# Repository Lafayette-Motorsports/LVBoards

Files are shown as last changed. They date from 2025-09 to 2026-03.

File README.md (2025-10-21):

# MotorsportsLVBoards

LV Board repository for Motorsports created 09.02.2025  

## BE SURE TO COMMIT & PUSH ALL CHANGES WHEN FINISHED TO KEEP THINGS UPDATED  

## Modulation
LV Boards are now 'modulated' - this means that each board is designed to serve a single purpose so that individual circuits/functions can be easily replaced  
    This means that wires need to be obviosuly labeled with their purpose and output params/types to keep things 'open source' enough that it can be easily updated -- keep documentation (wiring diagram, code comments, standalone documentation) updated, descriptive, and accurate  

## If this is your first time
To use this and work on the board (non cmd because if you don't know this you don't need to be trying to do it on the console):  
    - make a github account   
        - you can do this with your school email or your personal but if you plan on making changes, make your screen name traceable (eg. we want to be able to know who's doing stuff)  
    - download github for desktop (https://desktop.github.com/download/) and sign in  
    - 'follow' this repository to add it to your account  
    - click current repository (top left) --> add --> clone repository --> pull origin  
    - find your file path (repository --> show in explorer) and open whatever you want  
    - if you make changes, YOU NEED TO MANUALLY UPDATE THE REPOSITORY, ALL CHANGES MADE ARE LOCAL UNTIL THIS IS DONE  
        - go back to your github app and open the repository (its probably still open), add a summary and commit your changes, push to origin  
        - MAKE YOUR SUMMARY SOMEWHAT DETAILED, YOU DON'T NEED A PARAGRAPH BUT THIS IS A REALLY GOOD PLACE TO PUT A CHANGE LOG SO WE CAN TRACK WHATS HAPPENING WHEN AND GET A SOMEWHAT DETAILED HISTORY  

## Component Cacheing
When adding parts, store them as project-specific rather than global. You will need to create your own library for the project, but you should really only need to do it once per KiCad project -- this will make sure that projects are actually portable. Some projects were built without this in mind so be weary when trying to modify/process files -- they might not have footprints/symbols for every part. If you can't figure out how to do this (or you think you added a symbol but it's not working, footprint not loading, etc.) google it or ask -- the whole point of the GitHub is portability so its kind of stupid to ignore this.

for repository admin (or other) questions - Sean McLoughlin mclougsm@lafayette.edu

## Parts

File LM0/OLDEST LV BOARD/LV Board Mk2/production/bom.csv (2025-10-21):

Designator | Footprint | Quantity | Value | LCSC Part #
C1, C2, C3, C8 | CAP_CL32_SAM | 4 | 47u
C10, C11, C12, C17, C19, C9 | 0603 | 6 | 4.7u
C13, C14, C15, C16 | 1210 | 4 | 47u
C18, C31, C32, C33, C34, C35, C36, C37, C38, C4, C5, C6 | 1206 | 12 | 0.1u
C20, C21, C22 | 0603 | 3 | 22u
C23, C24, C25 | 1210 | 3 | 100u
C26 | 0603 | 1 | 0.22u
C27, C29, C30 | 0603 | 3 | 0.1n
C28 | 0603 | 1 | 27n
C7 | 1206 | 1 | 10u
CR1 | ZENER_Pair_15-5V_clamp | 1 | ESD12VD3B-TP
D1 | SOD323F_DIO | 1 | BZV55B15
D10, D11, D17, D18, D2, D3, D4, D5, D9 | Test-Yellow LED | 9 | LED (Test)
D12, D19, D20, D21, D22, D6 | D_DO-41_SOD81_P10.16mm_Horizontal | 6 | 1N4001
D13, D14, D7, D8 | IMD_ZENER | 4 | D_Zener
D15 | DIO_DFLS1100-7 | 1 | DFLS1100-7
D16 | POWERDI-123 | 1 | DFLS160Q-7
F1 | C1_BEL | 1 | C1Q 2A
F2 | FUSC6125X279N | 1 | 20A
H1, H2, H3, H4, H5, H6 | MountingHole_4mm_Pad_TopBottom | 6 | MountingHole_Pad
J1, J13, J14, J5, J6 | MOLEX_460150202 | 5 | Conn_01x02_Pin
J10, J11, J12, J15, J7, J8, J9 | PinHeader_1x02_P2.54mm_Vertical | 7 | Conn_01x02
J16 | PinHeader_1x02_P2.54mm_Vertical | 1 | Conn_01x02_Pin
J2, J3, J4 | AMPHENOL_L717SDA15P1ACH4F | 3 | L717SDA15P1ACH4F
K1 | RELAY_G6L-1P_DC5 | 1 | G6L-1P_DC5
K2 | RELAY_ALF1PF12 | 1 | ALF1PF12
K3, K4 | AHES4_PAN | 2 | AHES4291
L1 | glv_charge_inductor | 1 | 6.2u
MOSFET1, MOSFET2, MOSFET3, MOSFET4 | fan_driver | 4 | DMN3404L-7
Q1, Q2, Q3, Q4, Q5, Q6 | SOT23_INF | 6 | AON6411
R1, R10, R11, R13, R14, R15, R18, R21, R23, R27, R47, R50, R53, R56, R9 | 0603 | 15 | 10k
R12, R20, R22 | 0805 | 3 | 150R
R16, R17, R24, R25, R48, R49, R5, R51, R52, R54, R55, R57, R58, R6, R7, R8 | 0603 | 16 | 1k
R19 | 0603 | 1 | 2.2k
R2, R4 | 0603 | 2 | 57.6k
R26 | 0603 | 1 | 3.01k
R28, R29, R30, R31 | 1206 | 4 | 120
R3 | 0805 | 1 | 22k
R32 | 1206 | 1 | 0R
R33 | 0603 | 1 | 50k
R34 | 10m_sense | 1 | LVK12R010CER
R35, R36 | 0603 | 2 | 12k
R37, R42 | 0603 | 2 | 549k
R38 | 0603 | 1 | 86.6k
R39, R43, R44 | 1206 | 3 | 500k
R40 | 0603 | 1 | 113k
R41 | 0603 | 1 | 2.91k
R45, R46 | 1206 | 2 | 215k
SW1 | SW4_1825910-B_TEC | 1 | Test Reset IMD
SW2 | SW4_1825910-B_TEC | 1 | Test Reset AMS
TP1, TP2, TP3, TP4, TP5, TP6, TP7, TP8 | TestPoint_Loop_D2.60mm_Drill1.6mm_Beaded | 8 | TestPoint
U1, U2 | SOIC-8_3.9x4.9mm_P1.27mm | 2 | NE555D
U10, U12, U14, U16 | motorsports_senior_design_opto | 4 | TLP2745TP_E
U11, U13, U15, U9 | DBV5_TEX | 4 | UCC27517DBVR
U3 | REG_LT1117IST-5#PBF | 1 | LT1117-5.0
U4, U5, U6 | MOSFET_INFET | 3 | SI7116DN-T1-E3
U7 | UFD_28_ADI | 1 | LTC4013EUFD-TRPBF
U8 | LM324PWR | 1 | LM324PWR

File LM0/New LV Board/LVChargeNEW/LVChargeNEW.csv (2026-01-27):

Reference | Qty | Value | DNP | Exclude from BOM | Exclude from Board | Footprint | Datasheet
C1 | 1 | 1uF |  |  |  | Capacitor_THT:CP_Radial_D8.0mm_P5.00mm | ~
C2,C3 | 2 | 4.7uF |  |  |  | Capacitor_THT:CP_Radial_D8.0mm_P5.00mm | ~
C4,C6,C7 | 3 | 100uF |  |  |  | Capacitor_THT:CP_Radial_D8.0mm_P5.00mm | ~
C5,C9,C12,C16 | 4 | 80uF |  |  |  | Capacitor_THT:CP_Radial_D8.0mm_P5.00mm | ~
C8,C15 | 2 | 470nF |  |  |  | Capacitor_THT:CP_Radial_D8.0mm_P5.00mm | ~
C10,C11,C13,C14 | 4 | 100nF |  |  |  | Capacitor_THT:CP_Radial_D8.0mm_P5.00mm | ~
C_sys1,C_sys2,C_sys3,C_sys4,C_sys5,C_sys6,C_sys7,C_sys8,C_sys9 | 9 | 100u |  |  |  | Capacitor_SMD:C_1210_3225Metric_Pad1.33x2.70mm_HandSolder | ~
D1,D2,D3 | 3 | LED |  |  |  | LED_SMD:LED_1206_3216Metric | ~
J1,J2 | 2 | Conn_01x02 |  |  |  |  | ~
J3 | 1 | Conn_01x05_Socket |  |  |  | Connector_PinSocket_1.27mm:PinSocket_1x06_P1.27mm_Vertical | ~
L2 | 1 | SRP1770TA-150M |  |  |  | LVChargeNEWLocalFootprints:SRP1770TA_150M | SRP1770TA-150M
Q1,Q2,Q3,Q4 | 4 | CSD15380F3T |  |  |  | LVChargeNEWLocalFootprints:IAUZ20N08S5L300ATMA1
R1,R4 | 2 | 100k |  |  |  | Resistor_THT:R_Axial_DIN0204_L3.6mm_D1.6mm_P5.08mm_Horizontal | ~
R2 | 1 | 53.8k |  |  |  | Resistor_THT:R_Axial_DIN0204_L3.6mm_D1.6mm_P5.08mm_Horizontal | ~
R3 | 1 | 85.4k |  |  |  | Resistor_THT:R_Axial_DIN0204_L3.6mm_D1.6mm_P5.08mm_Horizontal | ~
R5 | 1 | 2.4 |  |  |  | Resistor_THT:R_Axial_DIN0204_L3.6mm_D1.6mm_P5.08mm_Horizontal | ~
R6 | 1 | 5.24k |  |  |  | Resistor_THT:R_Axial_DIN0204_L3.6mm_D1.6mm_P5.08mm_Horizontal | ~
R7,R8,R10,R11 | 4 | 10 |  |  |  | Resistor_THT:R_Axial_DIN0204_L3.6mm_D1.6mm_P5.08mm_Horizontal | ~
R9 | 1 | 30.31k |  |  |  | Resistor_THT:R_Axial_DIN0204_L3.6mm_D1.6mm_P5.08mm_Horizontal | ~
R12,R13,R20 | 3 | 249k |  |  |  | Resistor_THT:R_Axial_DIN0204_L3.6mm_D1.6mm_P5.08mm_Horizontal | ~
R14 | 1 | 133k |  |  |  | Resistor_THT:R_Axial_DIN0204_L3.6mm_D1.6mm_P5.08mm_Horizontal | ~
R15,R16,R17,R18 | 4 | 10k |  |  |  | Resistor_THT:R_Axial_DIN0204_L3.6mm_D1.6mm_P5.08mm_Horizontal | ~
R19 | 1 | 2.6K |  |  |  | Resistor_THT:R_Axial_DIN0204_L3.6mm_D1.6mm_P5.08mm_Horizontal | ~
R_bat_ac1,R_bat_sns1 | 2 | .005 |  |  |  | LVChargeNEWLocalFootprints:RESC2012X80N | ~
U1 | 1 | PQ25856QWRRVRQ1 |  |  |  | LVChargeNEWLocalFootprints:Q25856QWRRVRQ1 | https://www.ti.com/lit/gpn/bq25856-q1

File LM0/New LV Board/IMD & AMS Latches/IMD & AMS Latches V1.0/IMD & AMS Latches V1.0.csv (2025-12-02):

Reference | Qty | Value | DNP | Exclude from BOM | Exclude from Board | Footprint | Datasheet
D1,D2,D5,D6 | 4 | 1N4743A |  |  |  | motorsports:D_DO-41_SOD81_P3.81mm_Vertical_AnodeUp | ~
D3,D7 | 2 | 1N4001 |  |  |  | Diode_THT:D_DO-41_SOD81_P10.16mm_Horizontal | http://www.vishay.com/docs/88503/1n4001.pdf
D4,D8 | 2 | LED (Test) |  |  |  | LED_THT:LED_D3.0mm | ~
J2 | 1 | B12B-PH-K-S |  |  |  | Connector_JST:JST_PH_B12B-PH-K_1x12_P2.00mm_Vertical | B12B-PH-K-S
K1,K2,K3,K4,K5,K6 | 6 | A161CS12VDC.64 |  |  |  | motorsports:RELAY_A161CS12VDC.64
R1,R2 | 2 | 680 |  |  |  | Resistor_THT:R_Axial_DIN0207_L6.3mm_D2.5mm_P2.54mm_Vertical | ~
R3,R4 | 2 | 2.2k |  |  |  | Resistor_THT:R_Axial_DIN0207_L6.3mm_D2.5mm_P2.54mm_Vertical | ~
SW1,SW2 | 2 | Test Reset IMD |  |  |  | motorsports:pushButton | ~

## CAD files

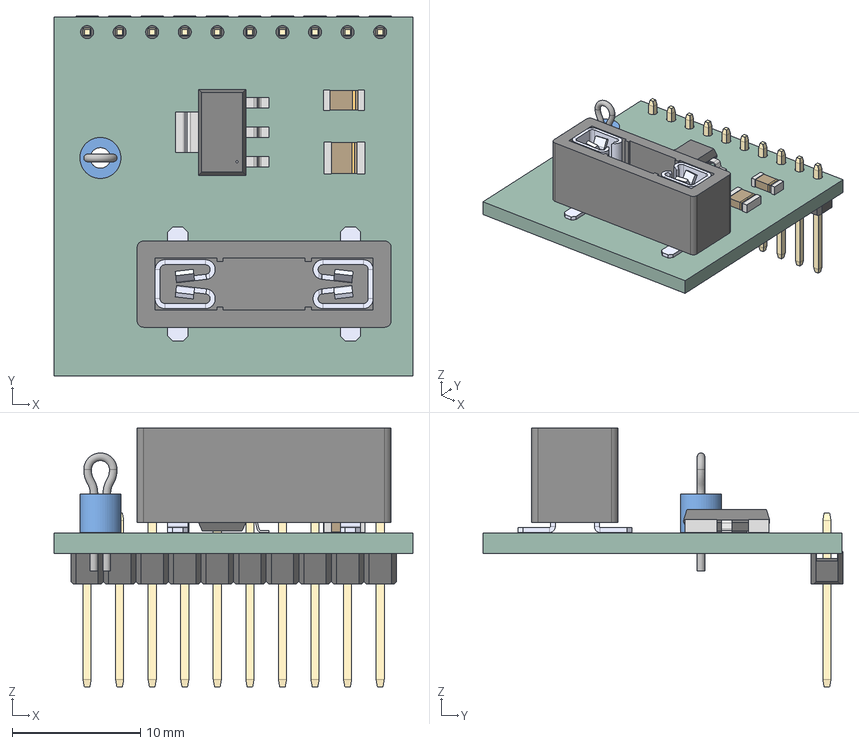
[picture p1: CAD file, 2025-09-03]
5V Converter/5V Converter V1.0/5V Converter.step
28.0 x 28.1 x 20.2 mm
TestPoint_Loop_D2_60mm_Drill1_6mm_Beaded_cp
3587TR
1x10 Male Pin Header
5V Converter_PCB

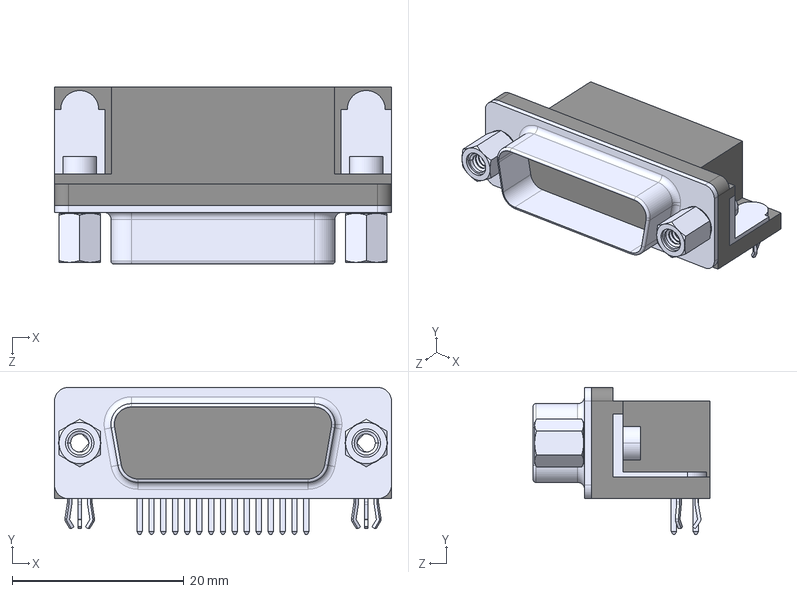
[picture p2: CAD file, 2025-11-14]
LM0/New LV Board/I-O Board V3.0/3d models/L717SDA15P1ACH4F--3DModel-STEP-554624.STEP
39.2 x 17.1 x 20.6 mm

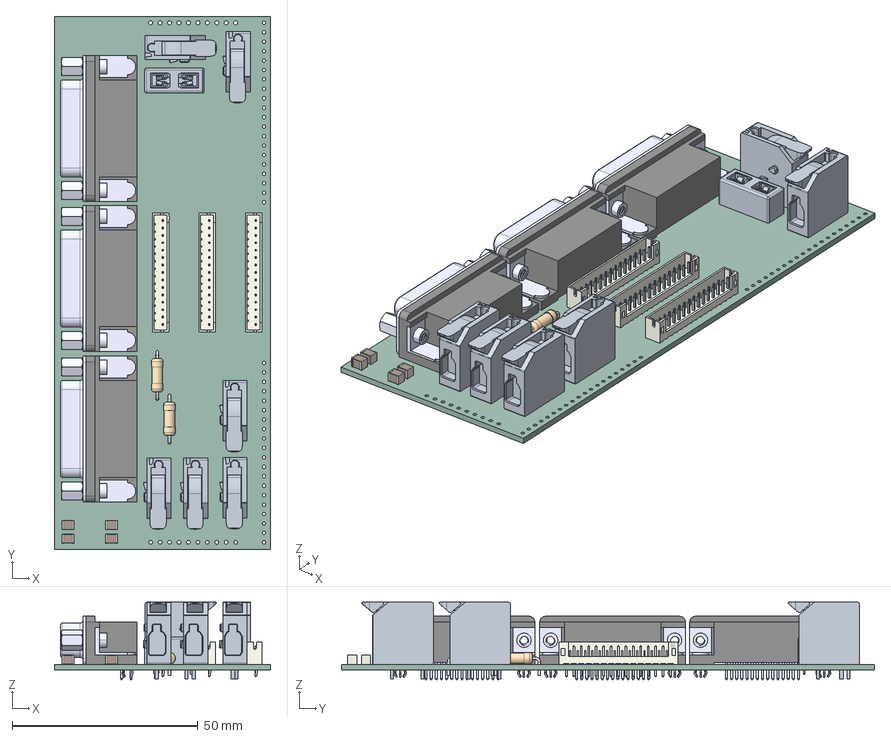
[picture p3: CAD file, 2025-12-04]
LM0/New LV Board/I-O Board V3.0/I-O Board V3.0.step
58.1 x 143.4 x 20.9 mm
C_1210_3225Metric x 4
JST_PH_B15B-PH-K_1x15_P2.00mm_Vertical x 3
l717sdxxxp1ach4f Body _15 x 3
R_Axial_DIN0309_L9.0mm_D3.2mm_P12.70mm_Horizontal x 2
F3568-1
3557_rev.C x 2
I-O Board V3.0_PCB

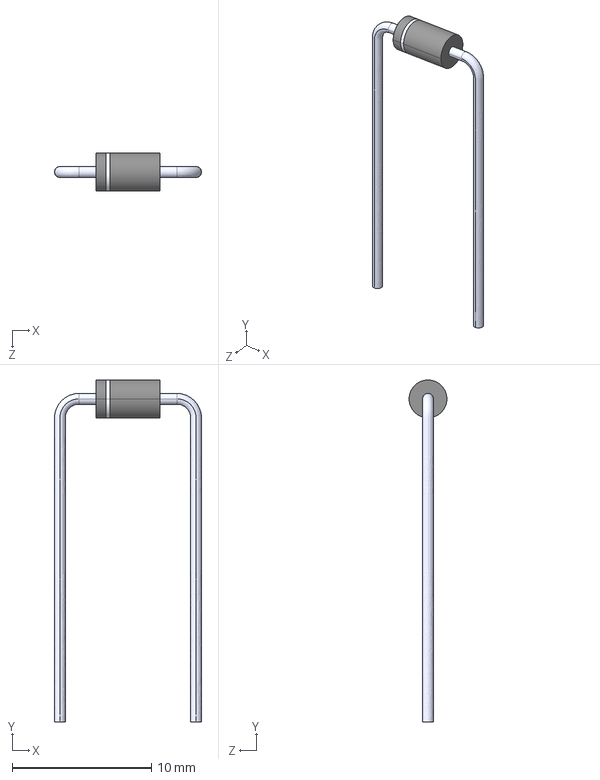
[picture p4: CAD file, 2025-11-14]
LM0/New LV Board/IMD & AMS Latches/IMD & AMS Latches V1.0/3d Models/1N4743A.step
10.6 x 24.6 x 2.72 mm

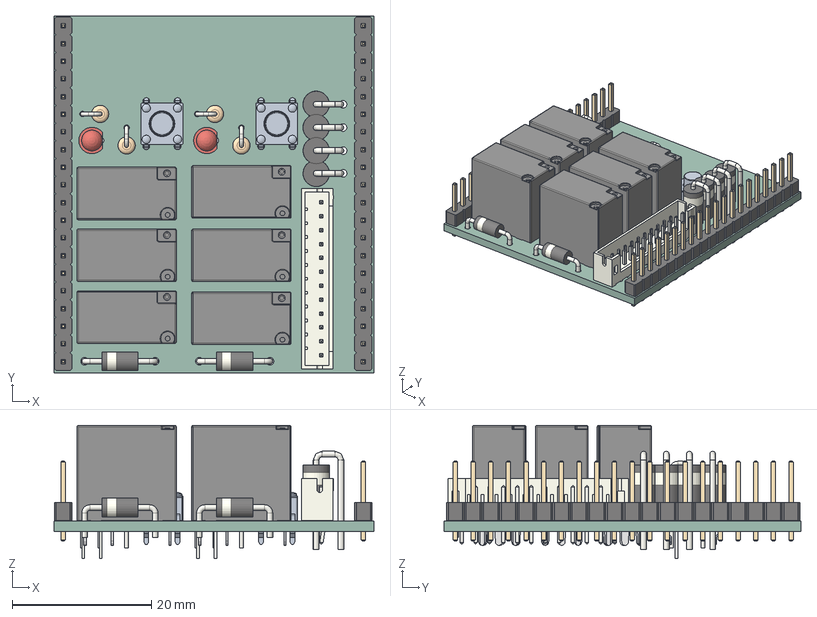
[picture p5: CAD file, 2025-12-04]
LM0/New LV Board/IMD & AMS Latches/IMD & AMS Latches V1.0/IMD & AMS Latches V1.0.step
46.0 x 51.3 x 19.2 mm
A16_Cover x 6
A16_TERMINAL_LG x 12
A16_TERMINAL_M x 6
A16_TERMINAL_SM x 12
Same_Sky_TS02-66-55-BK-160-LCR-D x 2
D_DO-41_SOD81_P10.16mm_Horizontal x 2
D_A-405_P2.54mm_Vertical_KathodeUp x 4
PinHeader_1x20_P2.54mm_Vertical x 2
LED_D3.0mm x 2
R_Axial_DIN0207_L6.3mm_D2.5mm_P2.54mm_Vertical x 4
JST_PH_B12B-PH-K_1x12_P2.00mm_Vertical
IMD & AMS Latches V1.0_PCB

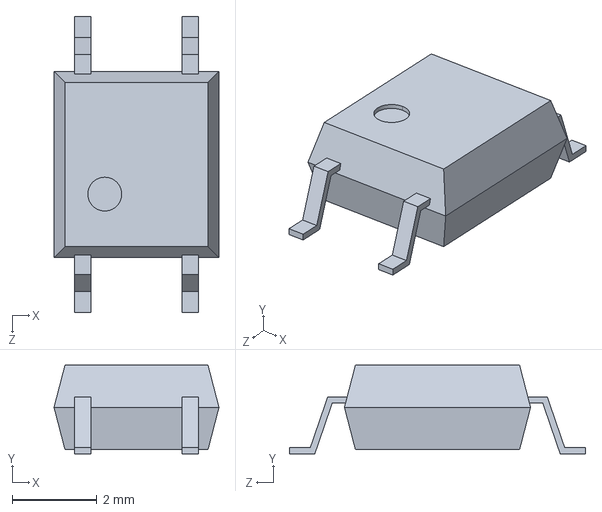
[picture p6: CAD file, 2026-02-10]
LM0/New LV Board/Precharge/G3VM_61G2.step
3.90 x 2.10 x 7.00 mm

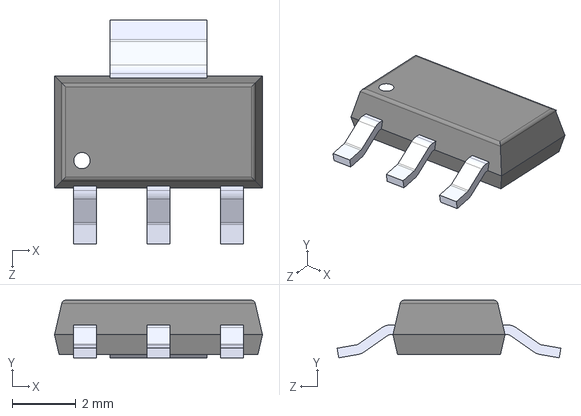
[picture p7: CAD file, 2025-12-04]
LM0/New LV Board/VCU MPR - 5V/VCU MPR - 5V V1.0/3-D Models/LT1117CST-5_TRPBF.step
6.50 x 1.80 x 7.00 mm

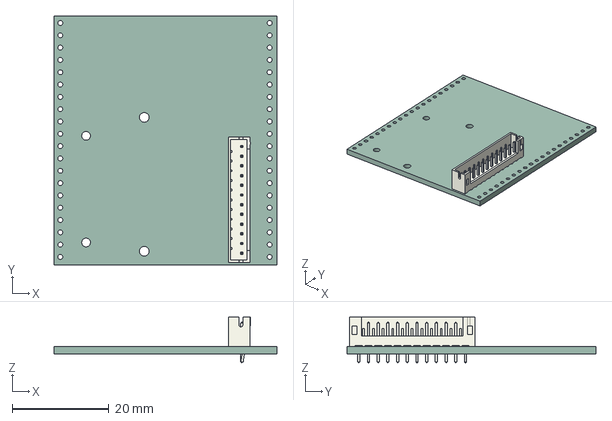
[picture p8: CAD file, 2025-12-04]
LM0/New LV Board/VCU MPR - 5V/VCU MPR - 5V V1.0/VCU MPR - 5V V1.0.step
46.0 x 51.3 x 9.40 mm
JST_PH_B12B-PH-K_1x12_P2.00mm_Vertical
VCU MPR - 5V V1.0_PCB

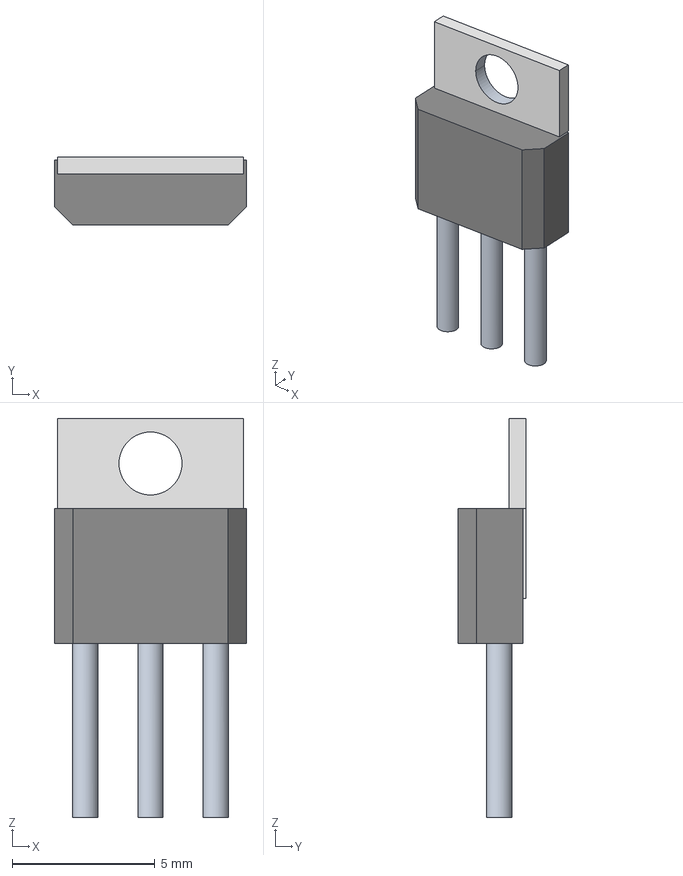
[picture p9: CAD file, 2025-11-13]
LM0/New LV Board/VCU Signals/VCU Signals V1.0/CAD 3D Models/DPAK-3_6P35X6P73_ONS.iges
6.73 x 2.39 x 14.0 mm

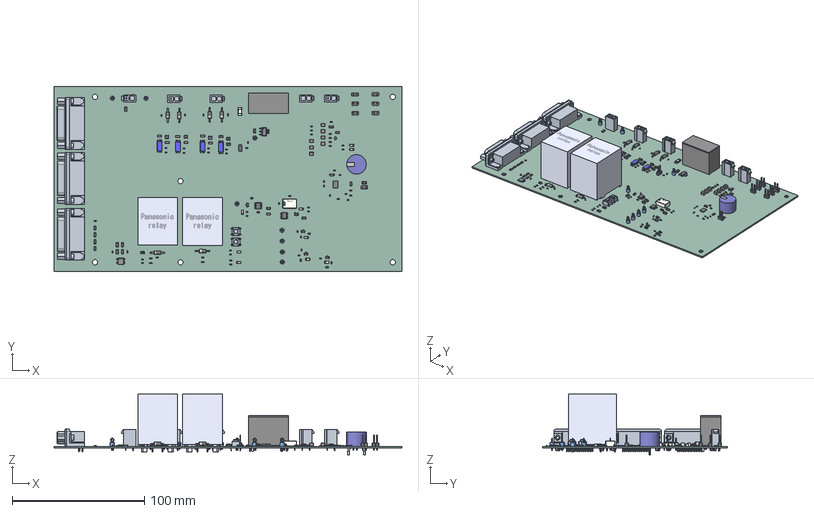
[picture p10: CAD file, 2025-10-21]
LM0/OLDEST LV BOARD/LV Board Mk2/LV Board Mk2.step
263.0 x 139.8 x 46.1 mm
LV Board Mk2 PCB

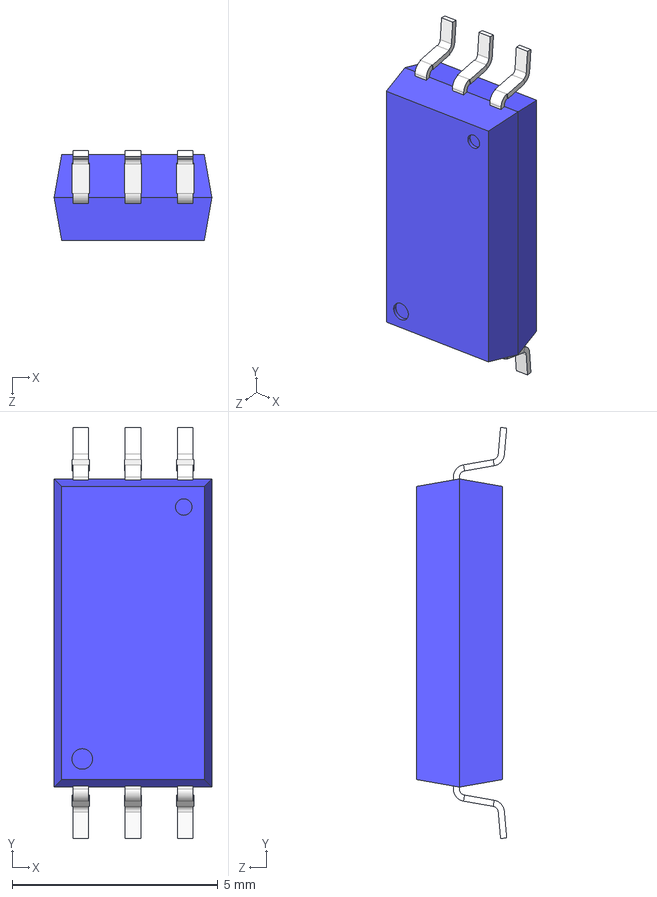
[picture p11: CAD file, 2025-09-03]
PWMs & Hall Effect Sensor/PAST VERSIONS/PWM Module V3.0B/PWM Module V3.0B (3)/PWM Module V3.0B/symbols&footprints/SO6L.step
3.84 x 10.00 x 2.20 mm

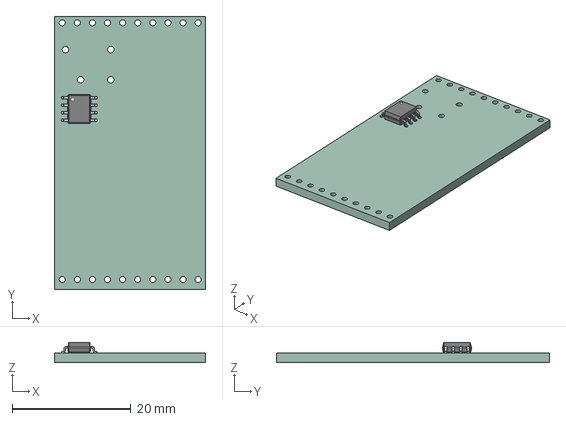
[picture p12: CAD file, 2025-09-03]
RTDS Timer/PAST VERSIONS/RTDS Control Module V3.0/RTDS Control Module V3.0/RTDS Control Module V3.0.step
25.4 x 46.0 x 3.40 mm
SOIC_8_39x49mm_P127mm
RTDS Control Module_PCB

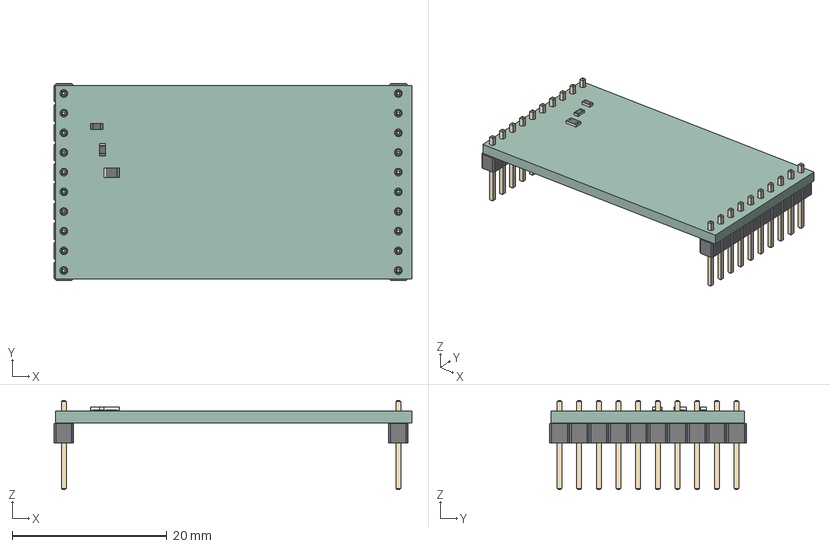
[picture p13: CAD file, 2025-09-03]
VCU Charge Status/PAST VERSIONS/VCU Charge Status Module V1.0/VCU Charge Status Module.step
46.2 x 25.4 x 11.5 mm
PinHeader_1x10_P254mm_Vertical x 2
R_0603_1608Metric x 2
R_0805_2012Metric
VCU Charge Status_PCB

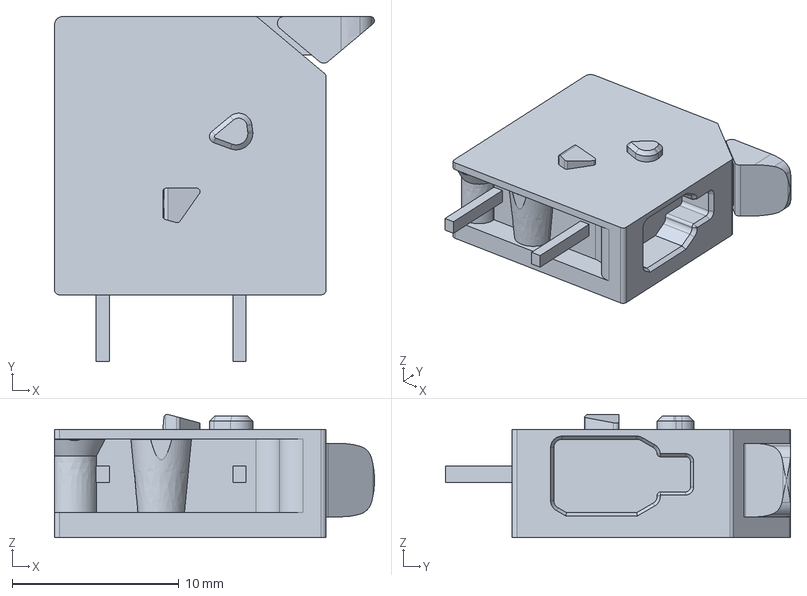
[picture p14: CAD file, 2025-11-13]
LM0/New LV Board/I-O Board V3.0/3d models/2604-1101.igs
19.2 x 20.7 x 7.40 mm

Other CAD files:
LM0/New LV Board/IMD & AMS Latches/IMD & AMS Latches V1.0/3d Models/A161C.stp
LM0/New LV Board/Traces/Traces V1.0/motorsports3dModels/3568.step
LM0/New LV Board/VCU MPR - 5V/VCU MPR - 5V V1.0/3-D Models/ALF1PF12.STEP
LM0/New LV Board/I-O Board V3.0/3d models/3568.step
LM0/New LV Board/I-O Board V3.0/3d models/2604-1101.stl
LM0/New LV Board/IMD & AMS Latches/IMD & AMS Latches V1.0/3d Models/Same_Sky_TS02-66-55-BK-160-LCR-D.step
LM0/New LV Board/Traces/Traces V1.0/motorsports3dModels/691137710002.step
LM0/New LV Board/Traces/Traces V1.0/motorsports3dModels/B12B-PH-K-S.step
LM0/New LV Board/Traces/Traces V1.0/motorsports3dModels/B15B-PH-K-S.step
LM0/New LV Board/VCU MPR - 5V/VCU MPR - 5V V1.0/3-D Models/3587.step
LM0/New LV Board/VCU MPR - 5V/VCU MPR - 5V V1.0/3-D Models/CL32B106KBJNNNE.step

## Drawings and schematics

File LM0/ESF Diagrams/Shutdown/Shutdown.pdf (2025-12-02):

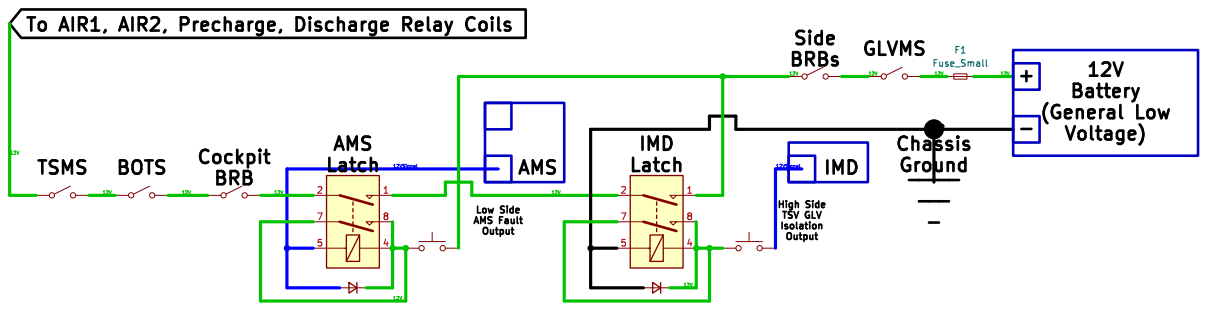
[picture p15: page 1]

High Side TSV GLV

Low Side AMS Fault Output

Id: 1/1 Title: File: Shutdown.kicad_sch Sheet: /

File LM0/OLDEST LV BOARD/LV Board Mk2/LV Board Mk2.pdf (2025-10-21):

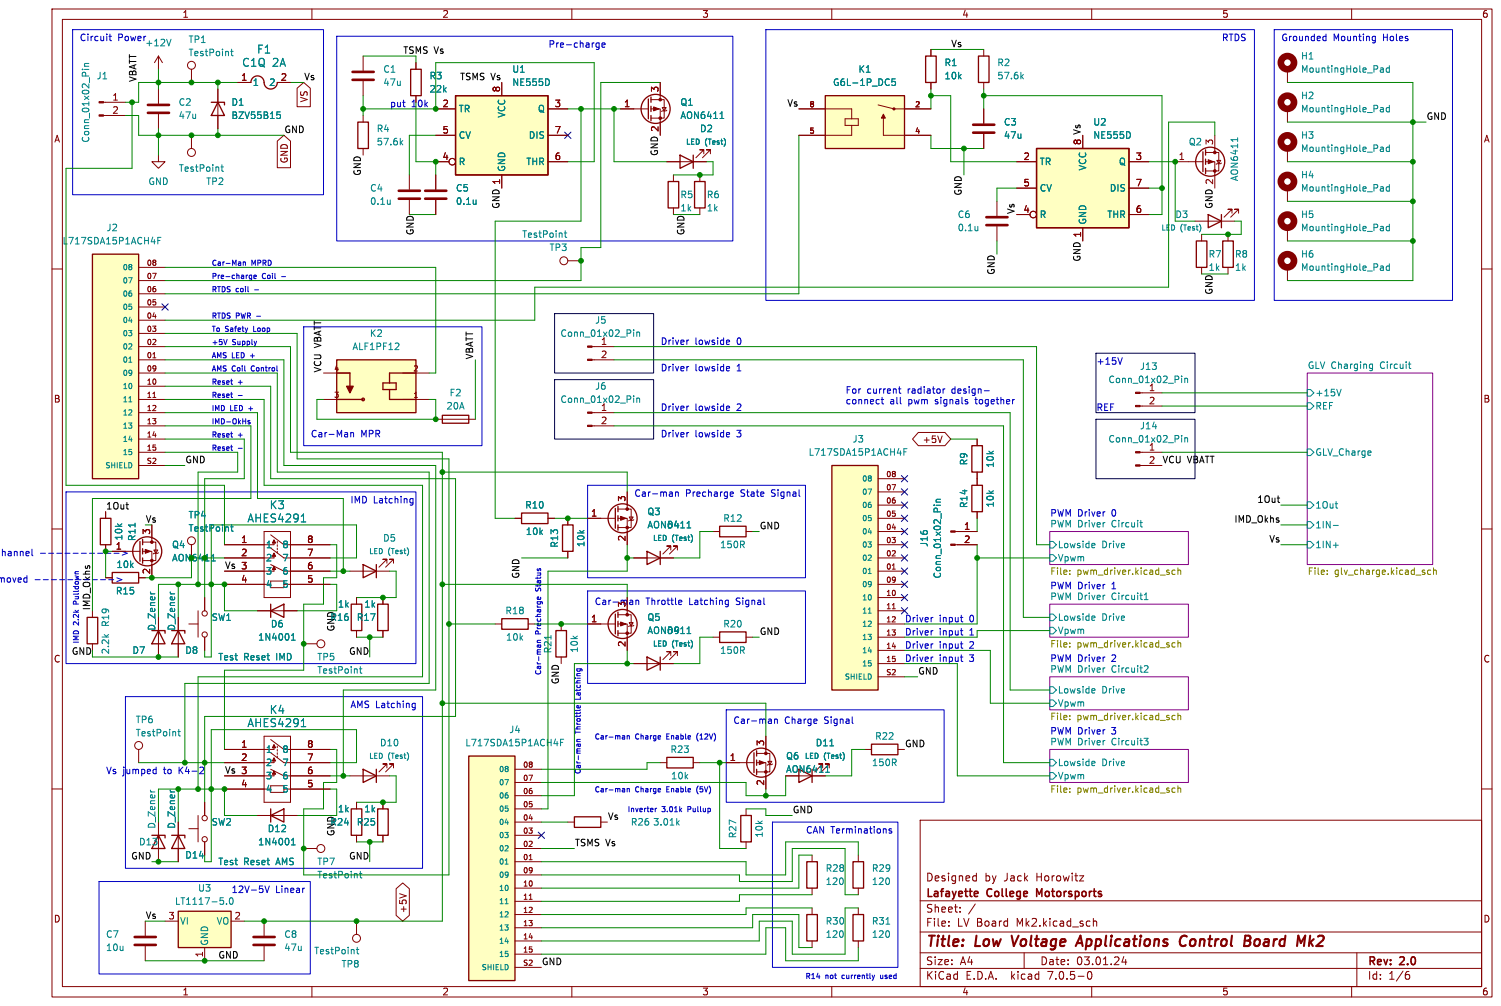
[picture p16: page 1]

1Out 1IN- 1IN+ GLV Charging Circuit File: glv_charge.kicad_sch

Lowside Drive PWM Driver Circuit File: pwm_driver.kicad_sch

Lowside Drive PWM Driver Circuit1 File: pwm_driver.kicad_sch

Lowside Drive PWM Driver Circuit2 File: pwm_driver.kicad_sch

Id: 1/6 Title: Low Voltage Applications Control Board Mk2

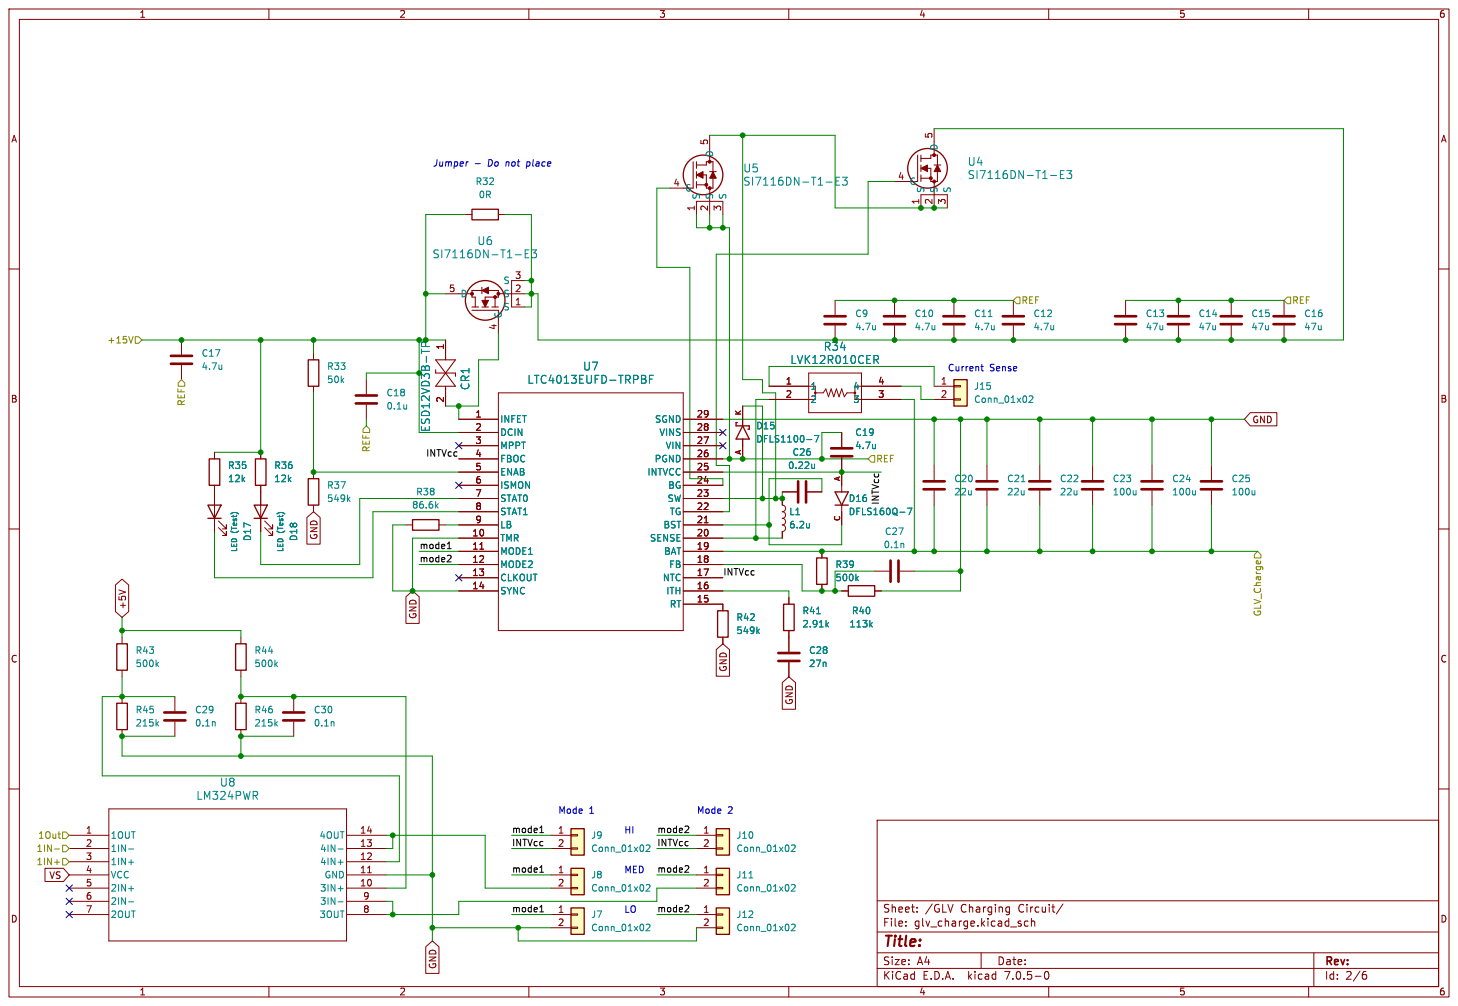
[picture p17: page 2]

LB 9 D18 LED (Test) D17 LED (Test) R35

Id: 2/6 Title: File: glv_charge.kicad_sch Sheet: /GLV Charging Circuit/ R43

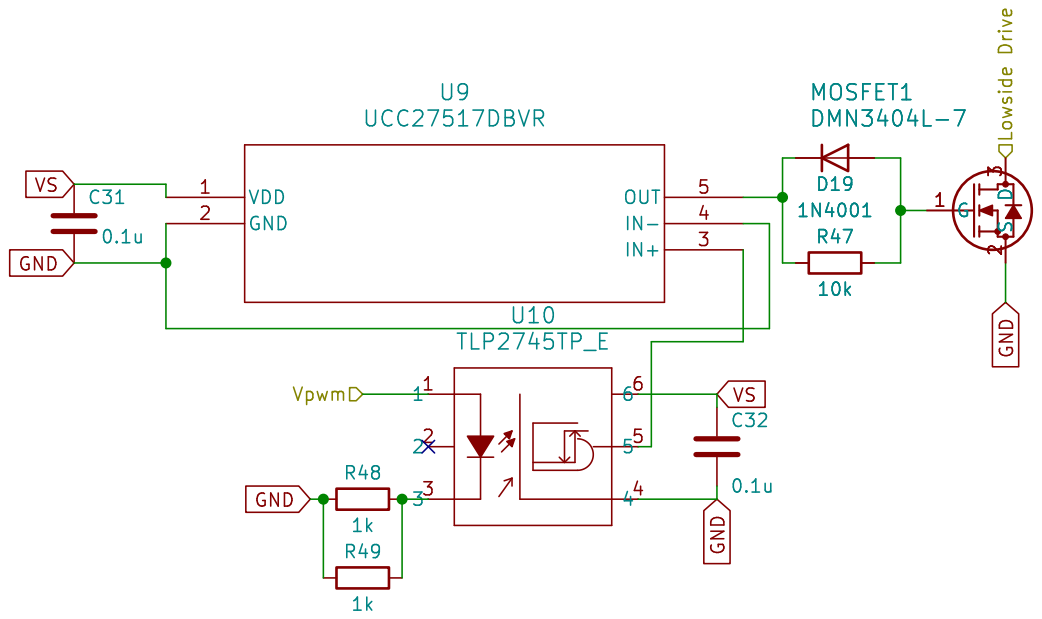
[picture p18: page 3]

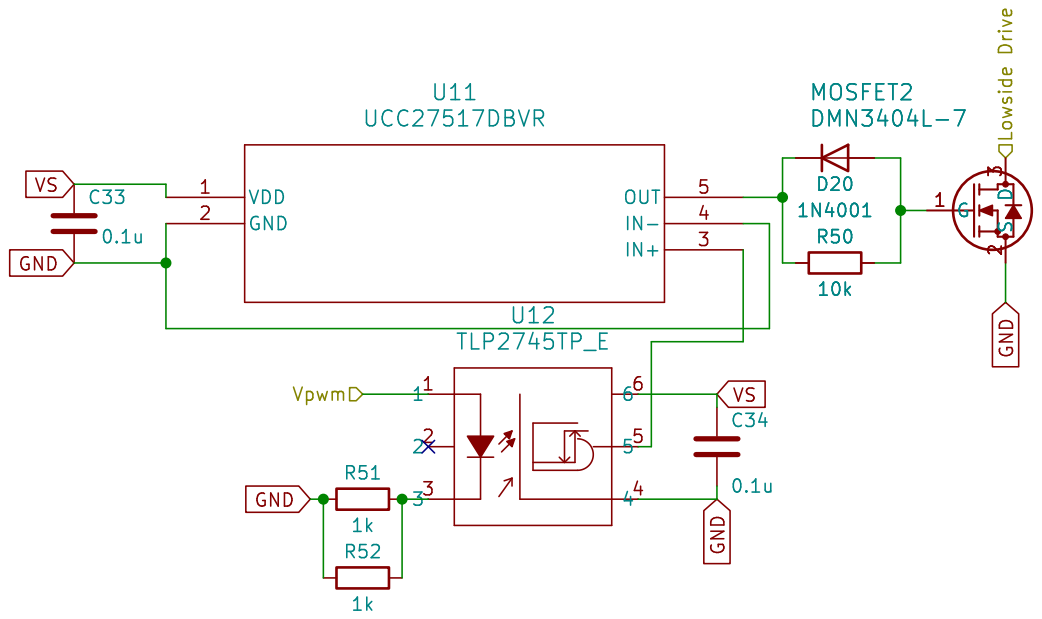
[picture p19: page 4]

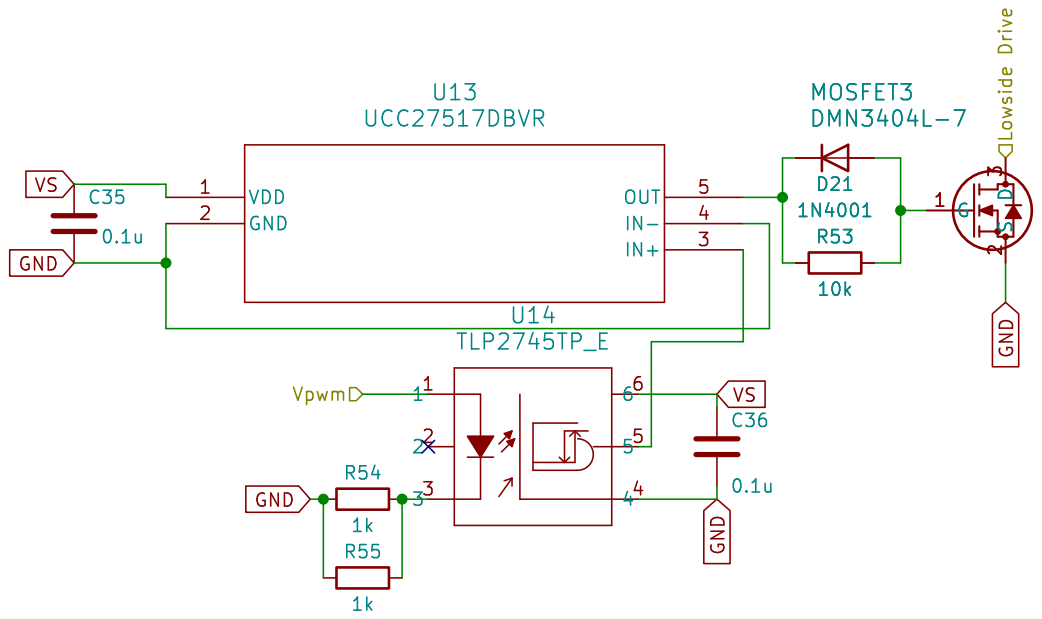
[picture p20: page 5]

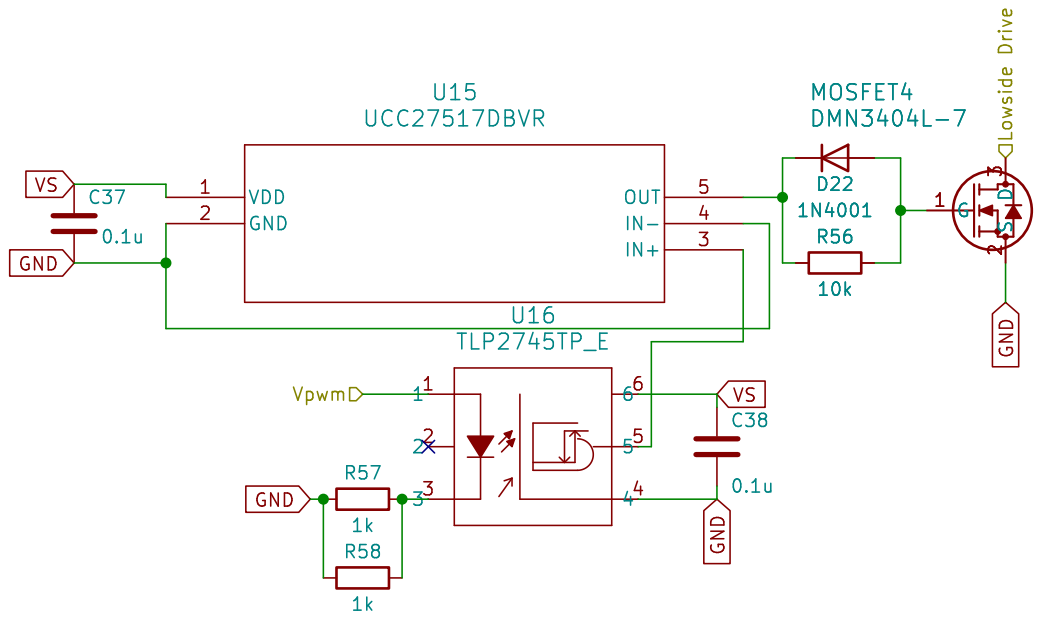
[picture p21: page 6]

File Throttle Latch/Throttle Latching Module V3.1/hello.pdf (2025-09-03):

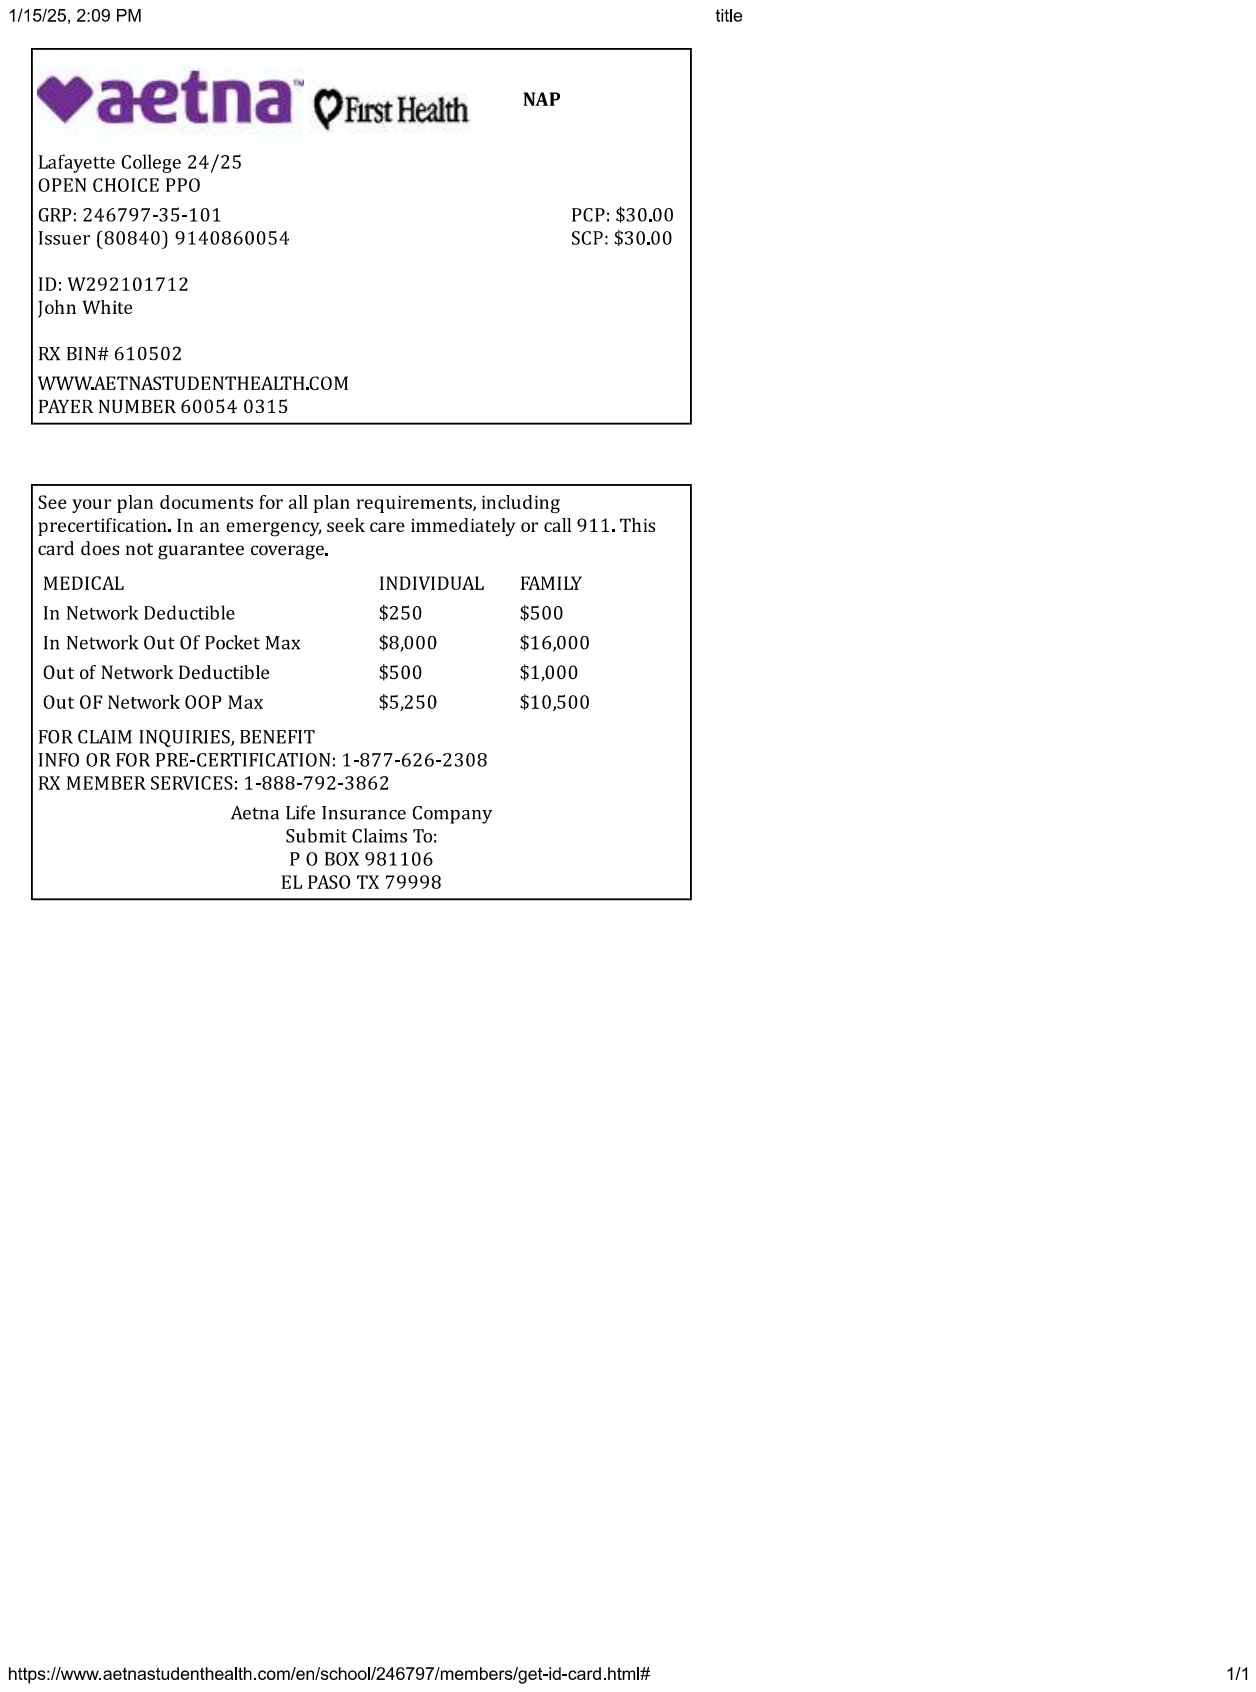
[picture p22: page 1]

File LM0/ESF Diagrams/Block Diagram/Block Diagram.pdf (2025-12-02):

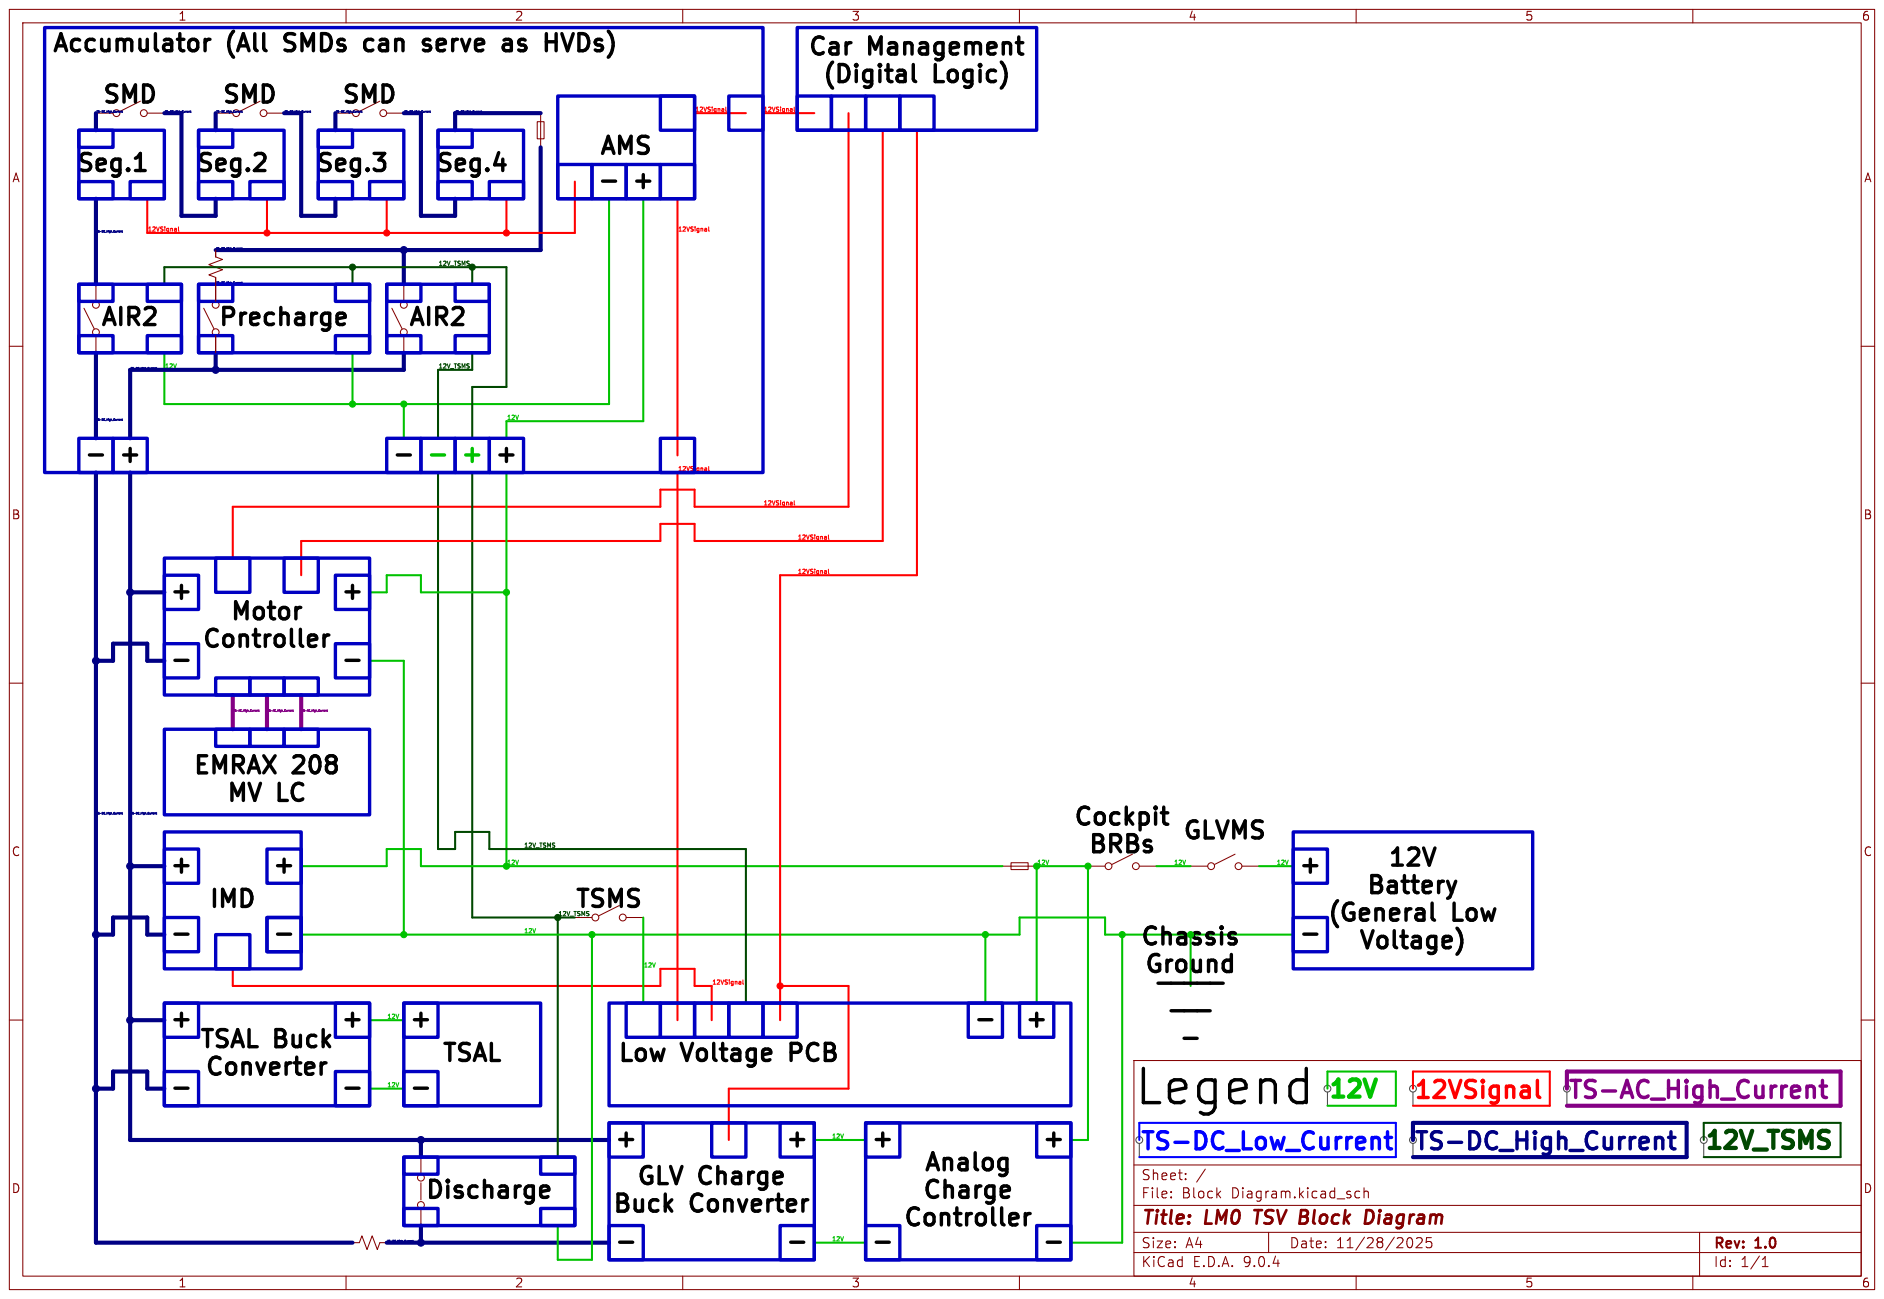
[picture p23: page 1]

Accumulator (All SMDs can serve as HVDs)
SMD

Id: 1/1 Title: LM0 TSV Block Diagram

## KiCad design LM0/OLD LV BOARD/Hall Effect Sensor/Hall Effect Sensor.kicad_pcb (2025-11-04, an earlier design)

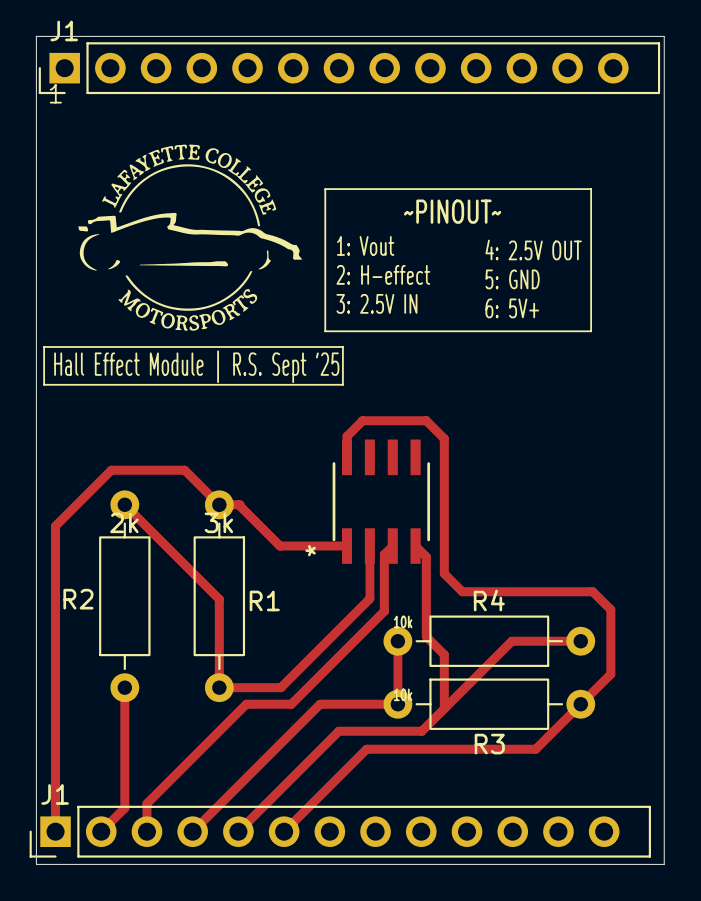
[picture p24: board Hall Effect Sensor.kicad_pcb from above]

Board: 2 copper layers, 34.9 x 46.0 mm, 7 parts (0 on the bottom side), 7 nets.

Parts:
J1, J1#2: PH1-20-UA; PinHeader_1x20_P2.54mm_Vertical
R1: 3k; R_Axial_DIN0207_L6.3mm_D2.5mm_P10.16mm_Horizontal
R2: 2k; R_Axial_DIN0207_L6.3mm_D2.5mm_P10.16mm_Horizontal
R3, R4: 10k; R_Axial_DIN0207_L6.3mm_D2.5mm_P10.16mm_Horizontal
opamp1: ADA4510-2ARZ; R-8_ADI

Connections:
+5V in: J1#2.6, R3.2, opamp1.8 (V+)
GND: J1#2.5, R4.1, opamp1.4 (V-)
Hall Effect Out: J1#2.2, R2.1
unnamed: R1.2, R2.2, opamp1.2 (INA-)
V(2.5)OUT: J1#2.4, R3.1, R4.2
V(2.5V)IN: J1#2.3, opamp1.3 (INA+)
Vout+: J1#2.1, R1.1, opamp1.1 (OUTA)

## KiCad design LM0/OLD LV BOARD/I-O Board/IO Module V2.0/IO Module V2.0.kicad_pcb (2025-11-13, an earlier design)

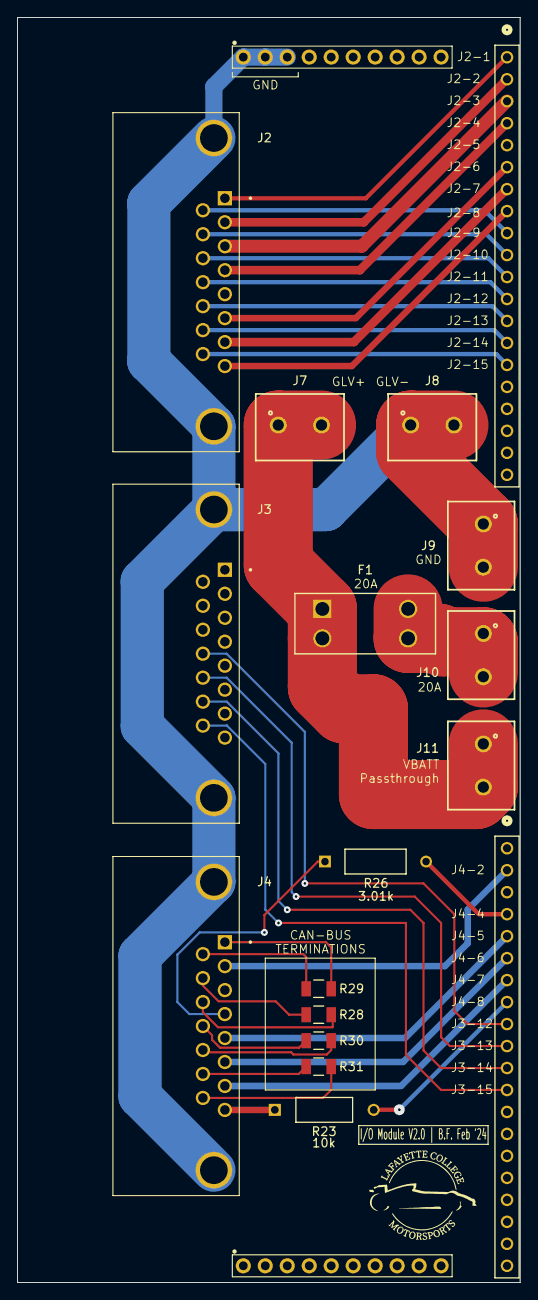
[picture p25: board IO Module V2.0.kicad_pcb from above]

Board: 2 copper layers, 58.1 x 146.2 mm, 18 parts (0 on the bottom side), 36 nets.

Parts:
F1: 20A; 3568_KEY
J1: PH1-10-UA; 1X10-2.54MM-THT
J2, J3, J4: *; AMPHENOL_L717SDA15P1ACH4F
J5, J6: 20-0600-21; CONN_20-0600-21_ARS
J7, J8, J9, J10, J11: 691137710002
R23: 10k; STA_CF14_STP
R26: 3.01k; YAG_MF25_YAG
R28, R29, R30, R31: 120; RES_TNPW1206_VIS

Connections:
unnamed: F1.1, F1.2, J7.1, J7.2, J11.1, J11.2
unnamed: F1.3, F1.4, J10.1, J10.2
unnamed: J1.1, J1.2, J1.3, J2.S1 (SHIELD), J2.S2 (SHIELD), J3.S1 (SHIELD), J3.S2 (SHIELD), J4.S1 (SHIELD), J4.S2 (SHIELD), J8.1, J8.2, J9.1, J9.2
unnamed: J2.01, J5.1
unnamed: J2.02, J5.2
unnamed: J2.03, J5.3
unnamed: J2.04, J5.4
unnamed: J2.06, J5.6
unnamed: J2.07, J5.7
unnamed: J2.08, J5.8
unnamed: J2.09, J5.9
unnamed: J2.10, J5.10
unnamed: J2.11, J5.11
unnamed: J2.12, J5.12
unnamed: J2.13, J5.13
unnamed: J2.14, J5.14
unnamed: J2.15, J5.15
unnamed: J3.12, J6.9
unnamed: J3.13, J6.10
unnamed: J3.14, J6.11
unnamed: J3.15, J6.12
unnamed: J4.01, R29.1
unnamed: J4.04, R26.1
unnamed: J4.05, J6.5
unnamed: J4.06, J6.6
unnamed: J4.07, J6.7
unnamed: J4.08, R23.1
unnamed: J4.09, R29.2
unnamed: J4.10, R28.1
unnamed: J4.11, R28.2
unnamed: J4.12, R30.1
unnamed: J4.13, R30.2
unnamed: J4.14, R31.1
unnamed: J4.15, R31.2
unnamed: J6.4, R26.2
unnamed: J6.8, R23.2

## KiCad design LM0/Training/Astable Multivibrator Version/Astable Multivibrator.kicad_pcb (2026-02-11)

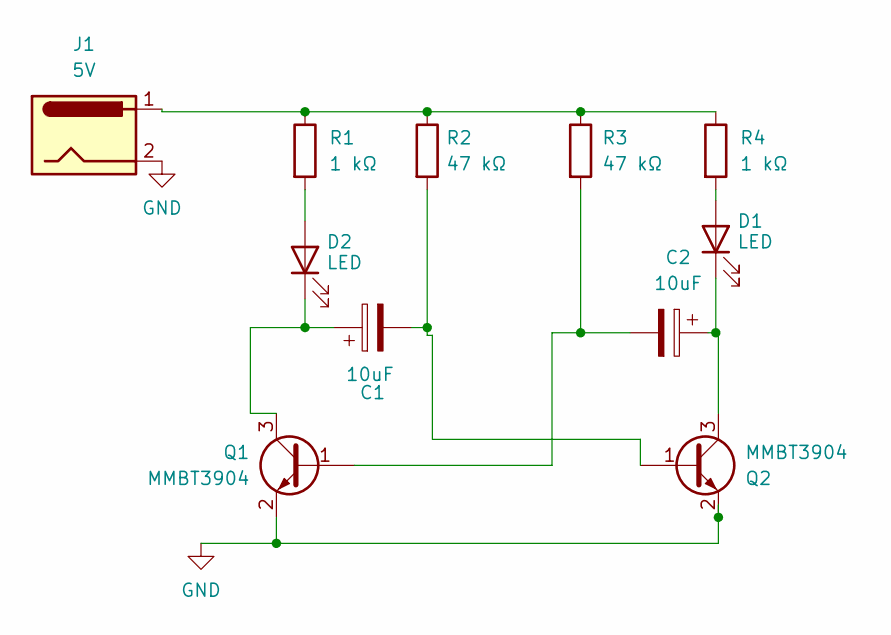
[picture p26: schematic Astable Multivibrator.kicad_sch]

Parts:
C1, C2: 10uF; CP_Radial_D5.0mm_P2.00mm
D1, D2: LED; LED_D5.0mm
J1: 5V; CUI_PJ-044A
Q1, Q2: MMBT3904; SOT-23
R1, R4: 1 kΩ; R_Axial_DIN0207_L6.3mm_D2.5mm_P10.16mm_Horizontal
R2, R3: 47 kΩ; R_Axial_DIN0207_L6.3mm_D2.5mm_P10.16mm_Horizontal

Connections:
GND: J1.2, Q1.2 (E), Q2.2 (E)
unnamed: D1.2 (A), R4.2
unnamed: C2.1, D1.1 (K), Q2.3 (C)
unnamed: D2.2 (A), R1.2
unnamed: C1.1, D2.1 (K), Q1.3 (C)
unnamed: J1.1, R1.1, R2.1, R3.1, R4.1
unnamed: C2.2, Q1.1 (B), R3.2
unnamed: C1.2, Q2.1 (B), R2.2

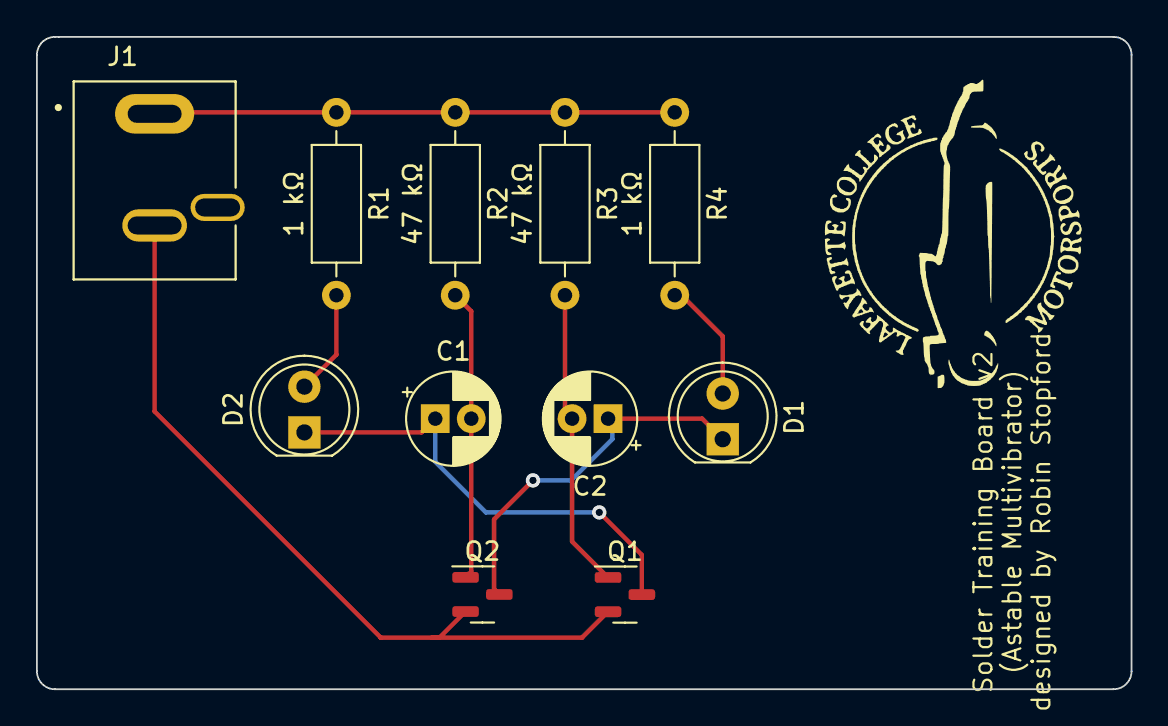
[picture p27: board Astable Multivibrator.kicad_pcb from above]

Board: 2 copper layers, 60.8 x 36.2 mm, 11 parts (0 on the bottom side), 8 nets.

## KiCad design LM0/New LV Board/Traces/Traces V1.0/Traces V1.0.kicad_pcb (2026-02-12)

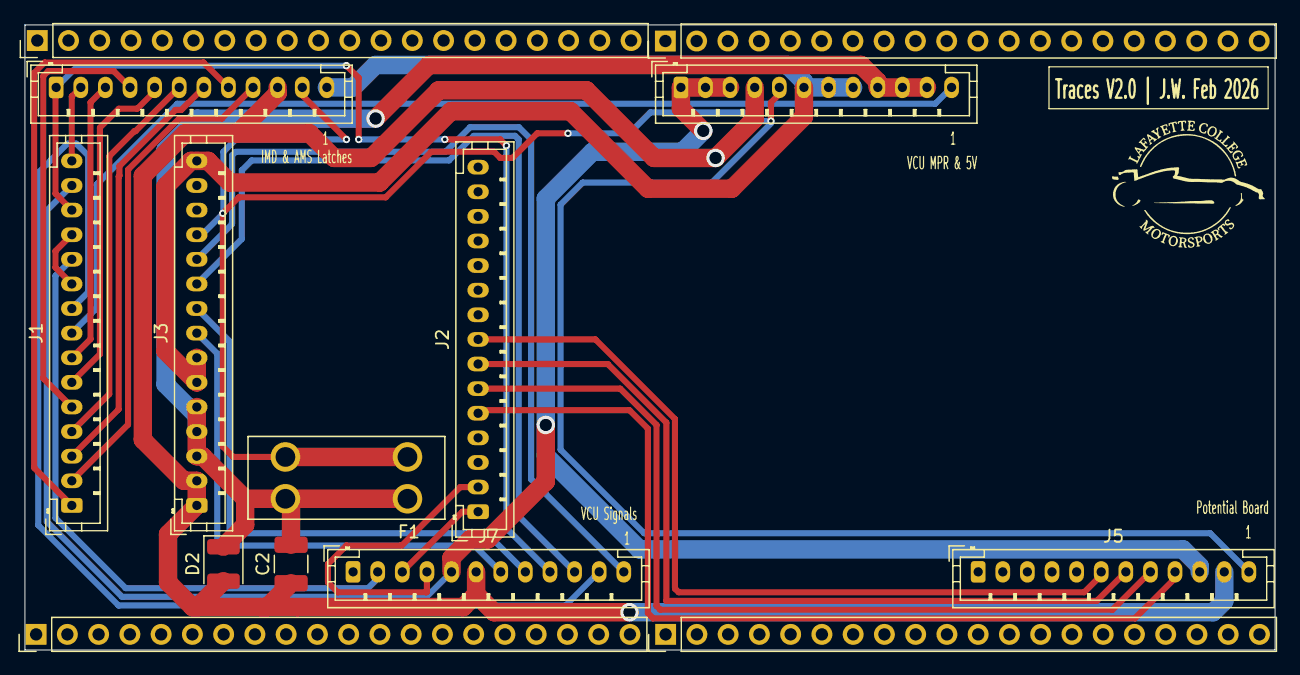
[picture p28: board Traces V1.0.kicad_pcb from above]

Board: 2 copper layers, 101.6 x 50.8 mm, 10 parts (0 on the bottom side), 28 nets.

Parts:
C2: 47u; C_1210_3225Metric_Pad1.33x2.70mm_HandSolder
D2: D_Zener; D_1210_3225Metric
F1: 2A; FUSE_3568
J1, J2, J3: B15B-PH-K-S; JST_PH_B15B-PH-K_1x15_P2.00mm_Vertical
J4, J5, J6, J7: B12B-PH-K-S; JST_PH_B12B-PH-K_1x12_P2.00mm_Vertical

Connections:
unnamed: C2.1, D2.2 (A), J3.1, J3.2, J4.4, J5.11, J6.10, J7.6
unnamed: C2.2, D2.1 (K), F1.1, F1.2, J3.3, J3.4, J3.5, J4.9, J4.10, J4.11
unnamed: J1.10, J1.12
unnamed: J1.14, J4.1, J4.2, J4.3, J5.10, J7.5
unnamed: F1.3, F1.4, J3.12, J4.5, J5.12, J6.11
unnamed: J3.6, J3.7, J3.15, J4.6, J4.7, J4.8, J6.12
unnamed: J1.8, J4.12
unnamed: J2.8, J5.6
unnamed: J2.7, J5.7
unnamed: J2.6, J5.8
unnamed: J2.5, J5.9
unnamed: J1.13, J6.1, J7.9
unnamed: J1.15, J6.2
unnamed: J1.7, J6.3
unnamed: J1.5, J6.4
unnamed: J1.6, J6.5
unnamed: J1.4, J6.6
unnamed: J1.3, J6.7
unnamed: J1.1, J6.8
unnamed: J1.2, J6.9
unnamed: J1.11, J7.2
unnamed: J2.1, J7.3
unnamed: J2.2, J7.4
unnamed: J3.8, J7.7
unnamed: J3.9, J7.8
unnamed: J3.10, J7.10
unnamed: J1.9, J7.11
unnamed: J3.11, J7.12

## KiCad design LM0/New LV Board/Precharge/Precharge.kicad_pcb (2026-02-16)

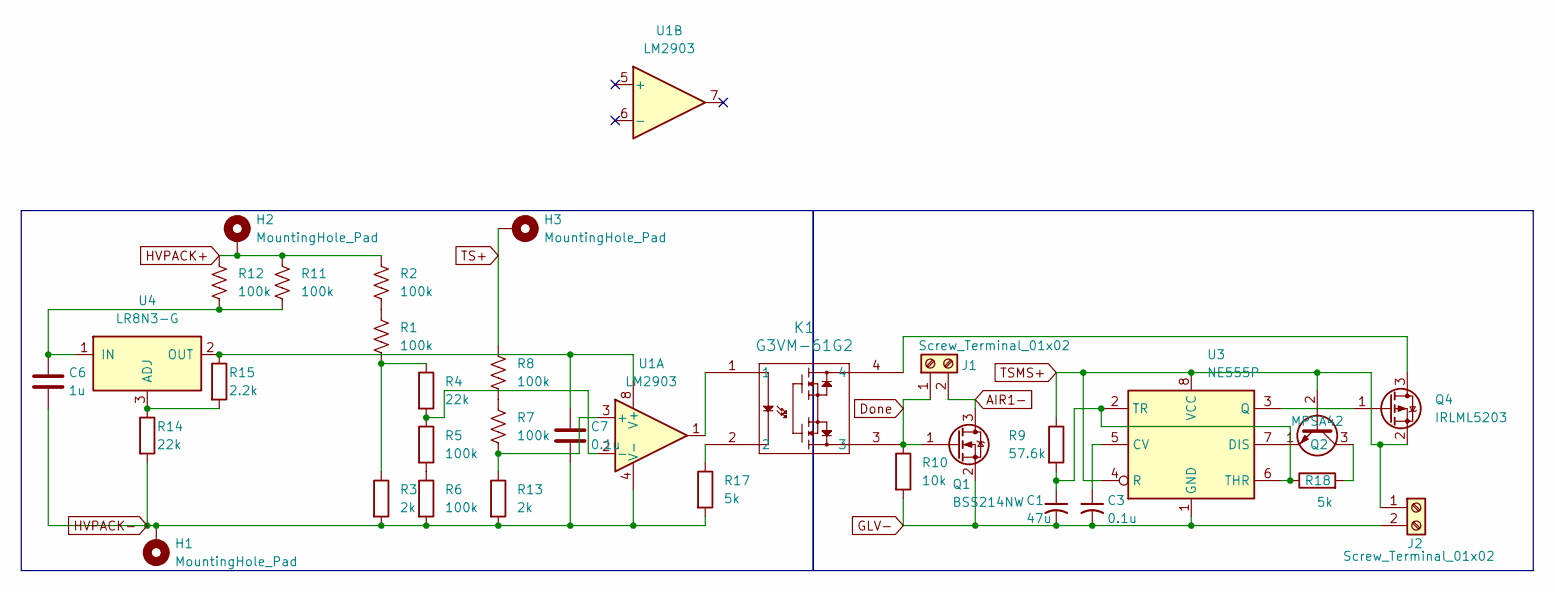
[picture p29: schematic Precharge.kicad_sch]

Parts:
C1: 47u; C_1210_3225Metric_Pad1.33x2.70mm_HandSolder
C3, C7: 0.1u; C_1206_3216Metric_Pad1.33x1.80mm_HandSolder
C6: 1u; C_1206_3216Metric_Pad1.33x1.80mm_HandSolder
H1, H2, H3: MountingHole_Pad; MountingHole_5.3mm_M5_DIN965_Pad
J1, J2: Screw_Terminal_01x02; TerminalBlock_MaiXu_MX126-5.0-02P_1x02_P5.00mm
K1: G3VM-61G2; G-SOP4_OMR
Q1: BSS214NW; SOT-323_SC-70_Handsoldering
Q2: MPSA42; TO-92
Q4: IRLML5203; SOT-23_Handsoldering
R1, R2, R7, R8: 100k; R_Axial_DIN0516_L15.5mm_D5.0mm_P5.08mm_Vertical
R3, R13: 2k; R_Axial_DIN0207_L6.3mm_D2.5mm_P2.54mm_Vertical
R4, R14: 22k; R_Axial_DIN0207_L6.3mm_D2.5mm_P2.54mm_Vertical
R5, R6: 100k; R_Axial_DIN0207_L6.3mm_D2.5mm_P2.54mm_Vertical
R9: 57.6k; R_Axial_DIN0207_L6.3mm_D2.5mm_P2.54mm_Vertical
R10: 10k; R_Axial_DIN0207_L6.3mm_D2.5mm_P2.54mm_Vertical
R11, R12: 100k; R_Axial_DIN0516_L15.5mm_D5.0mm_P7.62mm_Vertical
R15: 2.2k; R_Axial_DIN0207_L6.3mm_D2.5mm_P2.54mm_Vertical
R17, R18: 5k; R_Axial_DIN0207_L6.3mm_D2.5mm_P2.54mm_Vertical
U1: LM2903; DIP-8_W7.62mm
U3: NE555P; DIP-8_W7.62mm
U4: LR8N3-G; TO-92

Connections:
AIR1-: J1.2, Q1.3 (D)
Done: J1.1, K1.3, Q1.1 (G), R10.1
GLV-: C1.2, C3.2, J2.2, Q1.2 (S), R10.2, U3.1 (GND)
HVPACK+: H2.1, R2.1, R11.1, R12.1
HVPACK-: C6.2, C7.2, H1.1, R3.2, R6.2, R13.2, R14.2, R17.2, U1.4 (V-)
unnamed: K1.1, U1.1
unnamed: K1.2, R17.1
unnamed: Q2.3 (C), R18.2
unnamed: Q2.1 (E), U3.7 (DIS)
unnamed: K1.4, Q4.3 (D)
unnamed: Q4.1 (G), U3.3 (Q)
unnamed: R1.1, R2.2
unnamed: R1.2, R3.1, R4.1
unnamed: R5.2, R6.1
unnamed: R7.1, R8.2
unnamed: R7.2, R13.1, U1.3 (+)
unnamed: R4.2, R5.1, U1.2 (-)
unnamed: C7.1, R15.1, U1.8 (V+), U4.2 (OUT)
unnamed: C3.1, U3.5 (CV)
unnamed: C1.1, R9.2, R18.1, U3.2 (TR), U3.6 (THR)
unnamed: R14.1, R15.2, U4.3 (ADJ)
unnamed: C6.1, R11.2, R12.2, U4.1 (IN)
TS+: H3.1, R8.1
TSMS+: J2.1, Q2.2 (B), Q4.2 (S), R9.1, U3.4 (R), U3.8 (VCC)

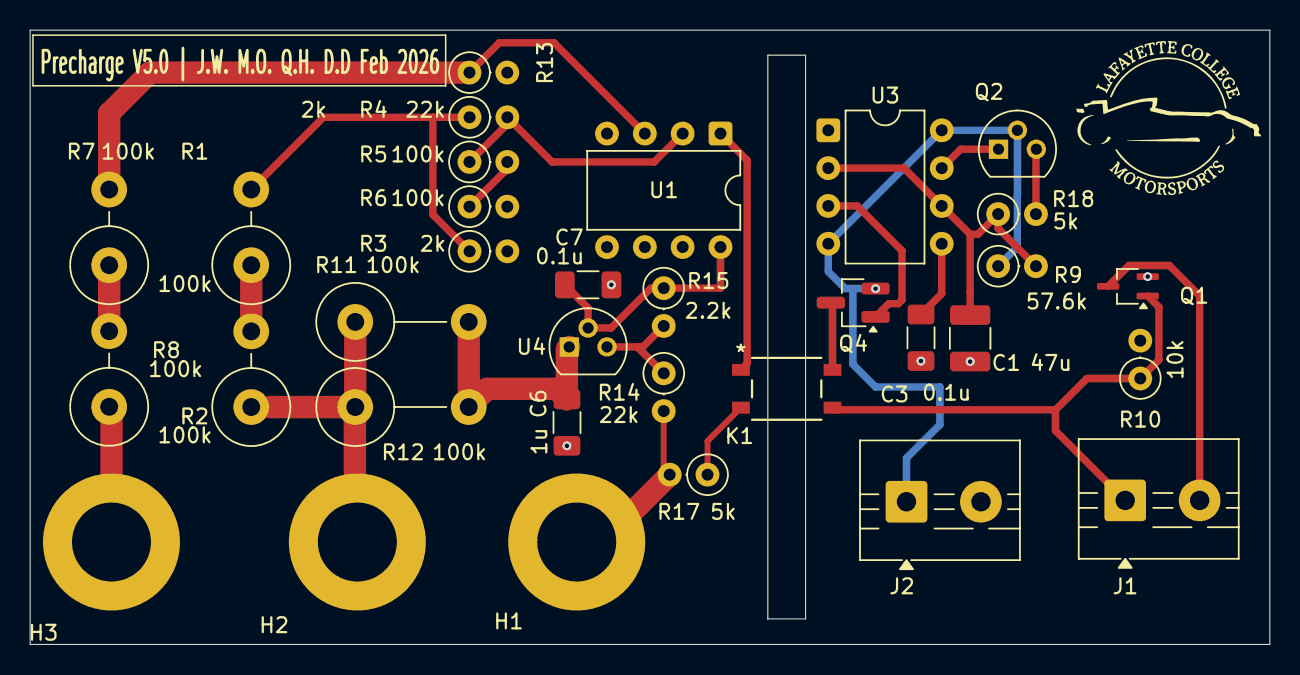
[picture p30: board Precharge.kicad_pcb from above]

Board: 2 copper layers, 83.2 x 41.2 mm, 33 parts (0 on the bottom side), 24 nets.

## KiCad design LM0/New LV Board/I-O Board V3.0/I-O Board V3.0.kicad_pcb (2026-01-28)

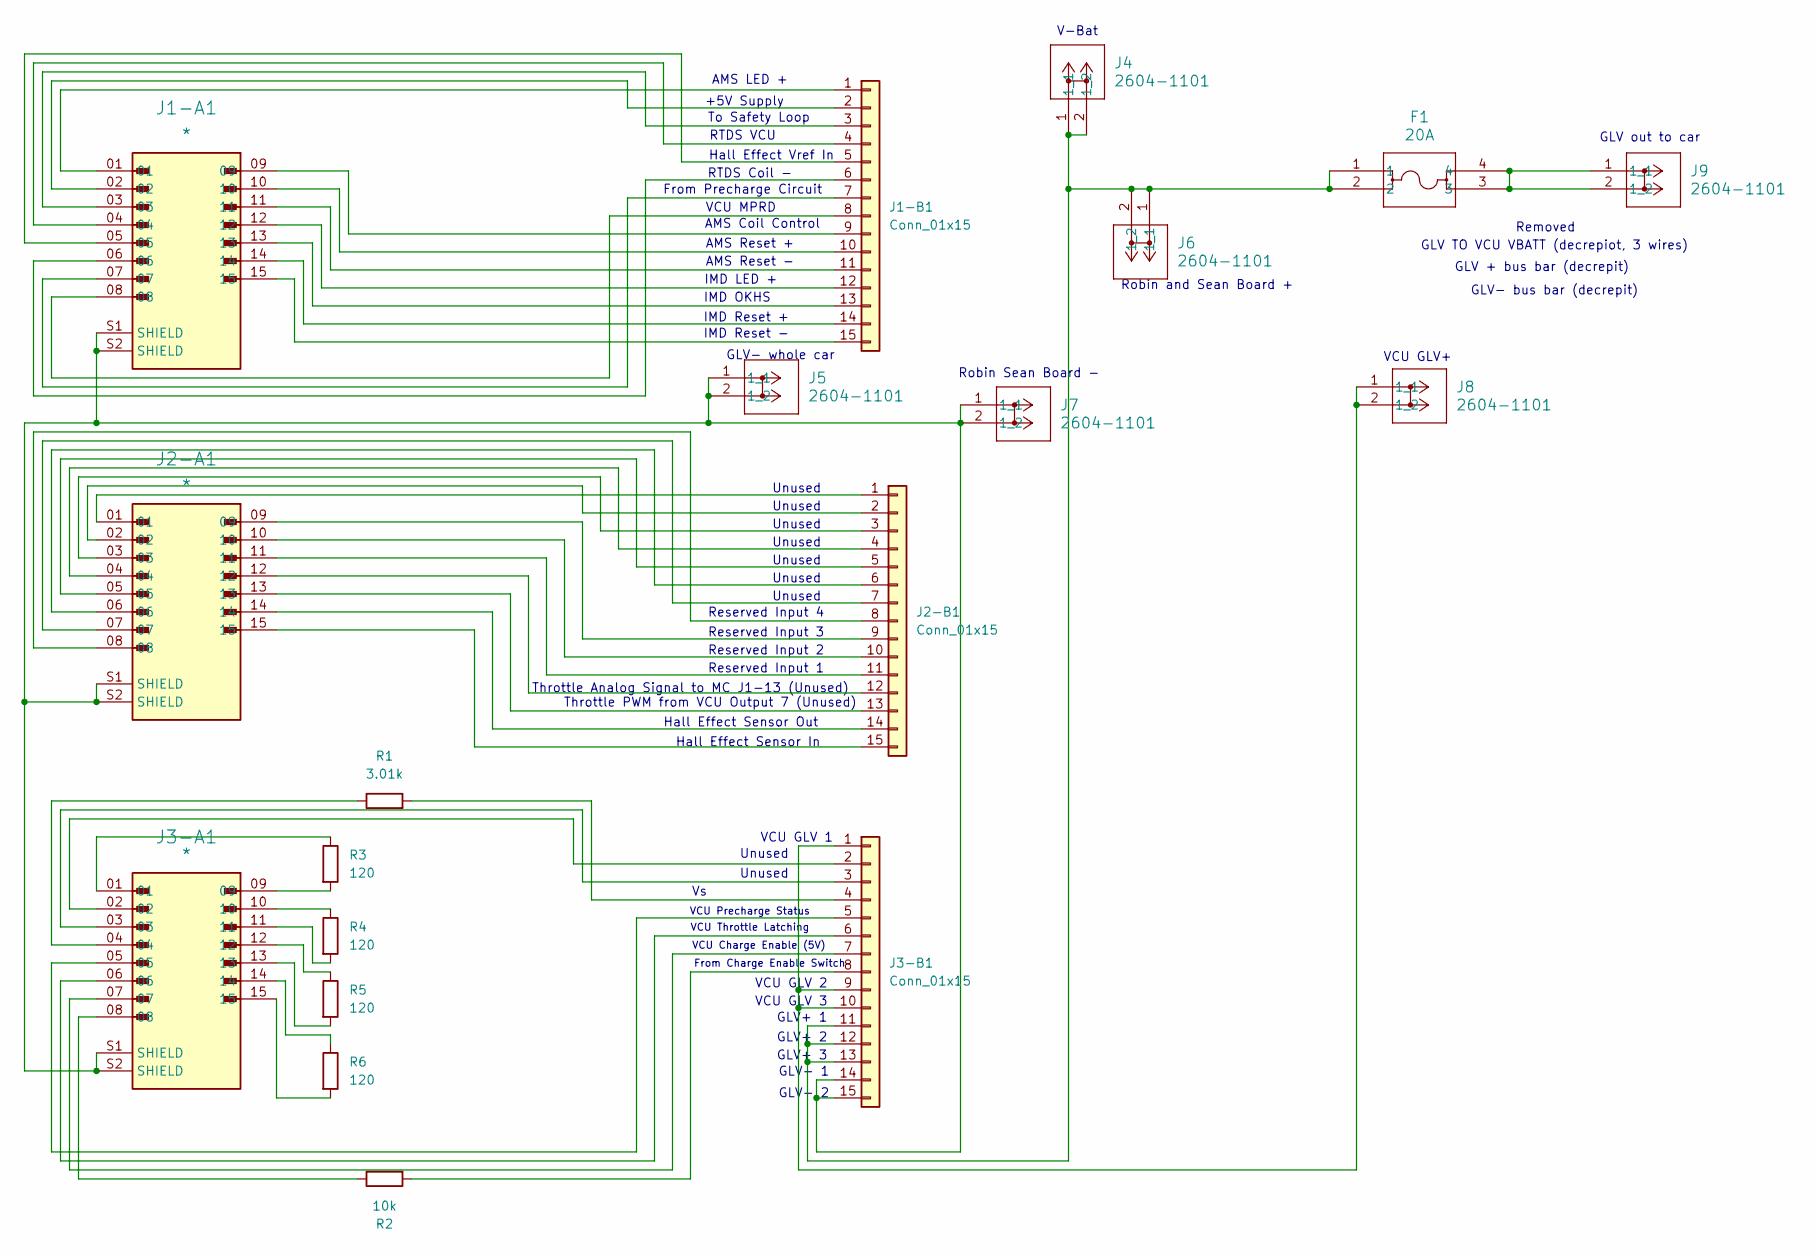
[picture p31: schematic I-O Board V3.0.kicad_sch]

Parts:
F1: 20A; 3568_KEY
J1-A1, J2-A1, J3-A1: *; AMPHENOL_L717SDA15P1ACH4F
J1-B1, J2-B1, J3-B1: Conn_01x15; JST_PH_B15B-PH-K_1x15_P2.00mm_Vertical
J4, J5, J6, J7, J8, J9: 2604-1101; CONN_2604-1101_WAG
R1: 3.01k; YAG_MF25_YAG
R2: 10k; YAG_MF25_YAG
R3, R4, R5, R6: 120; RESC3116X65N

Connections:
unnamed: J1-A1.01, J1-B1.1
unnamed: J1-A1.02, J1-B1.2
unnamed: J1-A1.03, J1-B1.3
unnamed: J1-A1.04, J1-B1.4
unnamed: J1-A1.05, J1-B1.5
unnamed: J1-A1.06, J1-B1.6
unnamed: J1-A1.07, J1-B1.7
unnamed: J1-A1.08, J1-B1.8
unnamed: J1-A1.09, J1-B1.9
unnamed: J1-A1.10, J1-B1.10
unnamed: J1-A1.11, J1-B1.11
unnamed: J1-A1.12, J1-B1.12
unnamed: J1-A1.13, J1-B1.13
unnamed: J1-A1.14, J1-B1.14
unnamed: J1-A1.15, J1-B1.15
unnamed: J2-A1.01, J2-B1.1
unnamed: J2-A1.02, J2-B1.2
unnamed: J2-A1.03, J2-B1.3
unnamed: J2-A1.04, J2-B1.4
unnamed: J2-A1.05, J2-B1.5
unnamed: J2-A1.06, J2-B1.6
unnamed: J2-A1.07, J2-B1.7
unnamed: J2-A1.08, J2-B1.8
unnamed: J2-A1.09, J2-B1.9
unnamed: J2-A1.10, J2-B1.10
unnamed: J2-A1.11, J2-B1.11
unnamed: J2-A1.12, J2-B1.12
unnamed: J2-A1.13, J2-B1.13
unnamed: J2-A1.14, J2-B1.14
unnamed: J2-A1.15, J2-B1.15
unnamed: J3-A1.01, R3.1
unnamed: J3-A1.04, R1.1
unnamed: J3-A1.08, R2.1
unnamed: J3-A1.09, R3.2
unnamed: J3-A1.10, R4.1
unnamed: J3-A1.11, R4.2
unnamed: J3-A1.12, R5.1
unnamed: J3-A1.13, R5.2
unnamed: J3-A1.14, R6.1
unnamed: J3-A1.15, R6.2
unnamed: J3-B1.1, J3-B1.9, J3-B1.10, J8.1, J8.2 (1)
unnamed: J3-A1.02, J3-B1.2
unnamed: J3-A1.03, J3-B1.3
unnamed: J3-B1.4, R1.2
unnamed: J3-A1.05, J3-B1.5
unnamed: J3-A1.06, J3-B1.6
unnamed: J3-A1.07, J3-B1.7
unnamed: J3-B1.8, R2.2
unnamed: F1.1, F1.2, J3-B1.11, J3-B1.12, J3-B1.13, J4.1, J4.2 (1), J6.1, J6.2 (1)
unnamed: J1-A1.S1 (SHIELD), J1-A1.S2 (SHIELD), J2-A1.S1 (SHIELD), J2-A1.S2 (SHIELD), J3-A1.S1 (SHIELD), J3-A1.S2 (SHIELD), J3-B1.14, J3-B1.15, J5.1, J5.2 (1), J7.1, J7.2 (1)
unnamed: F1.3, F1.4, J9.1, J9.2 (1)

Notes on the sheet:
V-Bat
AMS LED +
+5V Supply
VCU GLV 2
Unused
Reserved Input 2
IMD Reset -
IMD Reset +
VCU MPRD
GLV+ 3
IMD OKHS
Reserved Input 1
GLV+ 2
RTDS Coil -
VCU Charge Enable (5V)
GLV- whole car
Unused
GLV + bus bar (decrepit)
To Safety Loop
Removed
VCU GLV+
Robin Sean Board -
GLV- bus bar (decrepit)
Hall Effect Sensor Out
GLV- 1
Hall Effect Vref In
AMS Coil Control
From Charge Enable Switch
AMS Reset +
Robin and Sean Board +
GLV- 2
GLV TO VCU VBATT (decrepiot, 3 wires)
VCU GLV 1
Throttle PWM from VCU Output 7 (Unused)
Hall Effect Sensor In
VCU GLV 3
Throttle Analog Signal to MC J1-13 (Unused)
From Precharge Circuit
VCU Throttle Latching
Reserved Input 3

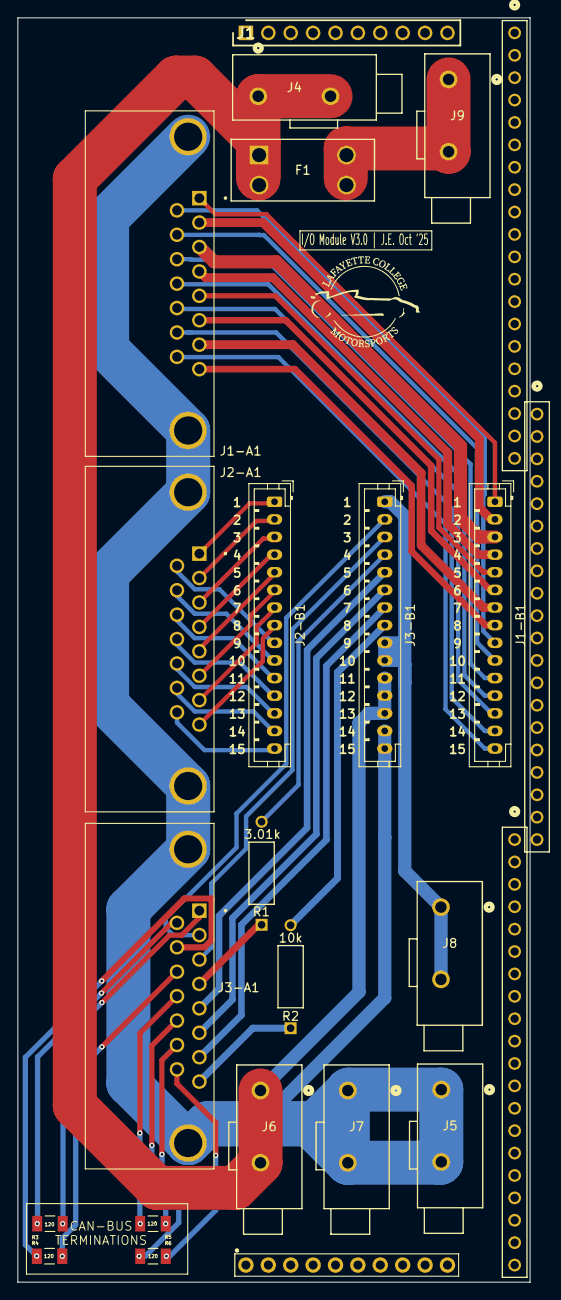
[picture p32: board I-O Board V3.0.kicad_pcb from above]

Board: 2 copper layers, 58.1 x 143.4 mm, 24 parts (0 on the bottom side), 51 nets.

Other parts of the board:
J1: PH1-10-UA; HDRV10W64P0X254_1X10_2540X249X886P
PH2, PH2#2, PH3: 20-0600-21; CONN_20-0600-21_ARS
PH4: 1X10-2.54MM-THT

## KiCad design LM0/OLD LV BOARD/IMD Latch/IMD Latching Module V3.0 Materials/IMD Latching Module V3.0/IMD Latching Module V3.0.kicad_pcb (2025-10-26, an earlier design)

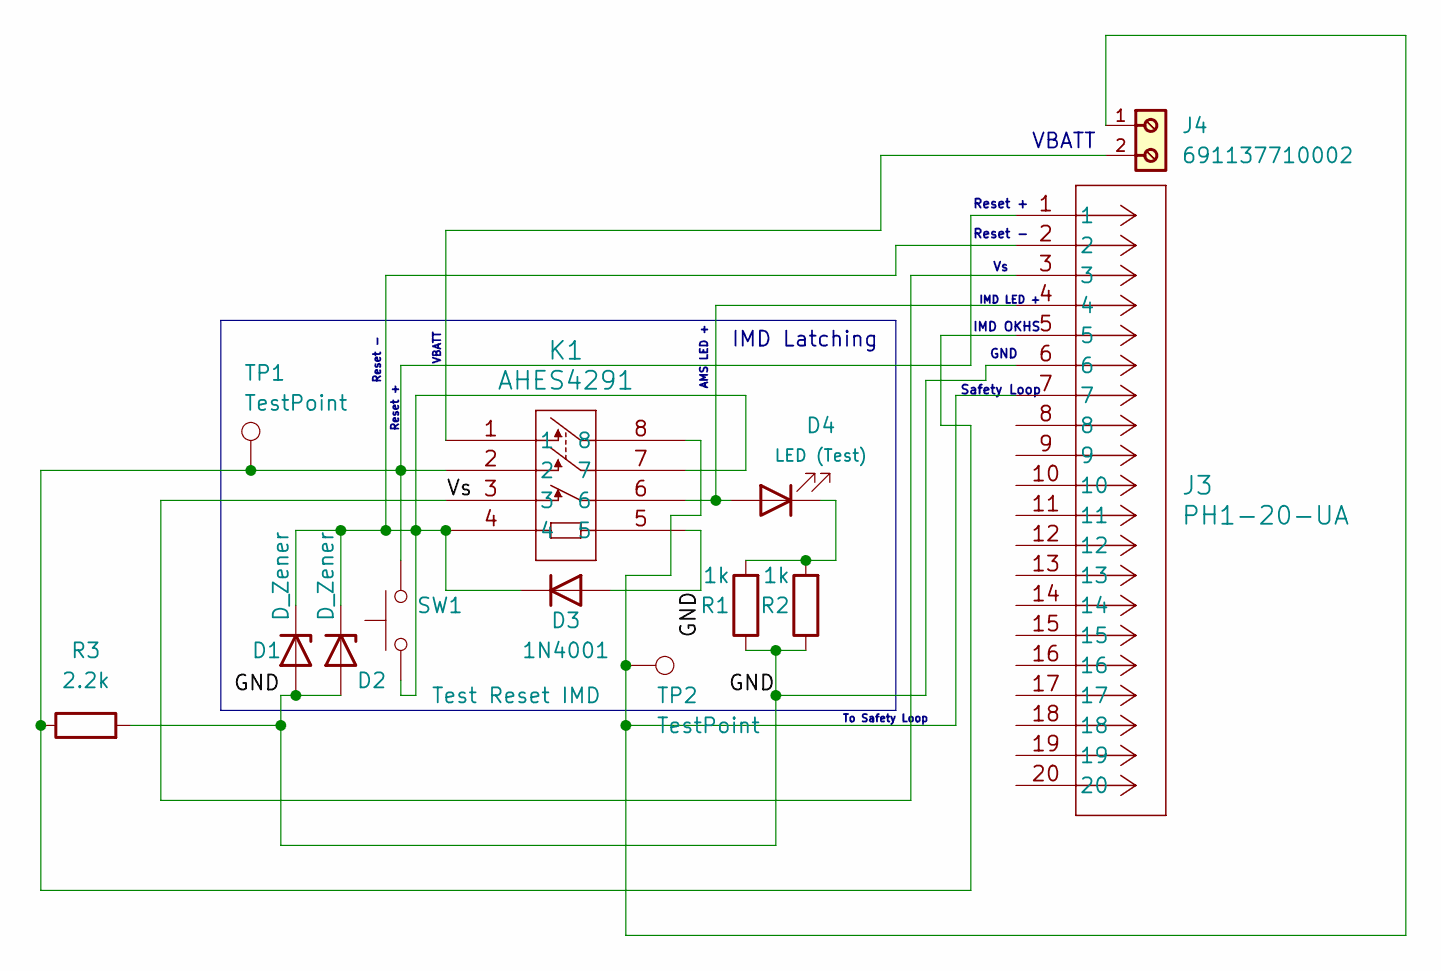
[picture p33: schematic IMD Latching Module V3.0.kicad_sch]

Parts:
D1, D2: D_Zener; RESC1508X55N
D3: 1N4001; D_DO-41_SOD81_P10.16mm_Horizontal
D4: LED (Test); LED_AP3216SYD_KNB-L
J3: PH1-20-UA; CONN_PH1-20-UA_ADM
J4: 691137710002; PART-NUMBER 691137710002
K1: AHES4291; AHES4_PAN
R1, R2: 1k; STA_CF14_STP
R3: 2.2k; STA_CF14_STP
SW1: Test Reset IMD; SW4_1825910-B_TEC
TP1, TP2: TestPoint; TestPoint_Loop_D2.60mm_Drill1.6mm_Beaded

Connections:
/GND: D1.2 (A), D2.2 (A), D3.2 (A), J3.6, K1.5, R1.1, R2.1, R3.2
/Vs: J3.3, K1.3
unnamed: D1.1 (K), D2.1 (K), D3.1 (K), J3.2, K1.4, K1.7, SW1.1
unnamed: D4.2 (A), J3.4, K1.6
unnamed: D4.1 (K), R1.2, R2.2
unnamed: J3.1, J3.5, K1.2, R3.1, SW1.2, TP1.1
unnamed: J3.7, J4.1, K1.8, TP2.1
unnamed: J4.2, K1.1

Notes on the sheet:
VBATT
IMD LED +
To Safety Loop
IMD OKHS
Reset -
Reset +
AMS LED +
Safety Loop
GND
IMD Latching

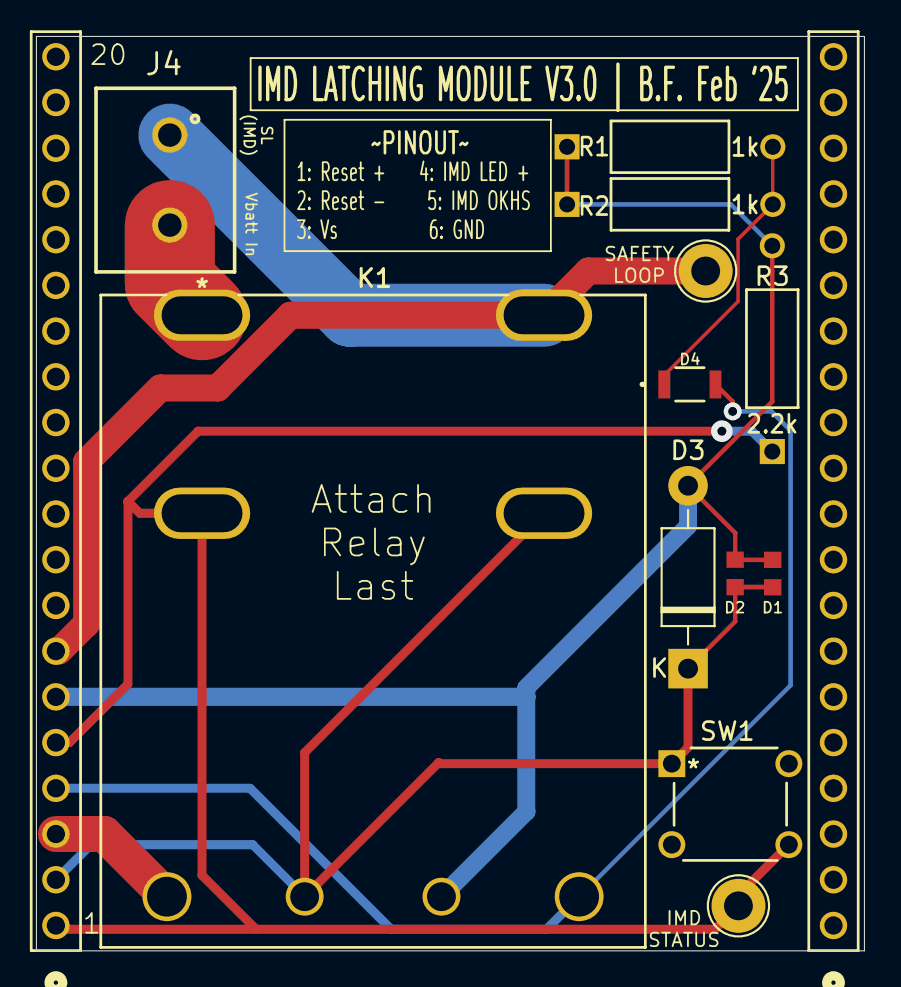
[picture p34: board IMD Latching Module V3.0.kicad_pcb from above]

Board: 2 copper layers, 46.0 x 50.8 mm, 14 parts (0 on the bottom side), 8 nets.

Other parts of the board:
J2: PH1-20-UA; CONN_PH1-20-UA_ADM

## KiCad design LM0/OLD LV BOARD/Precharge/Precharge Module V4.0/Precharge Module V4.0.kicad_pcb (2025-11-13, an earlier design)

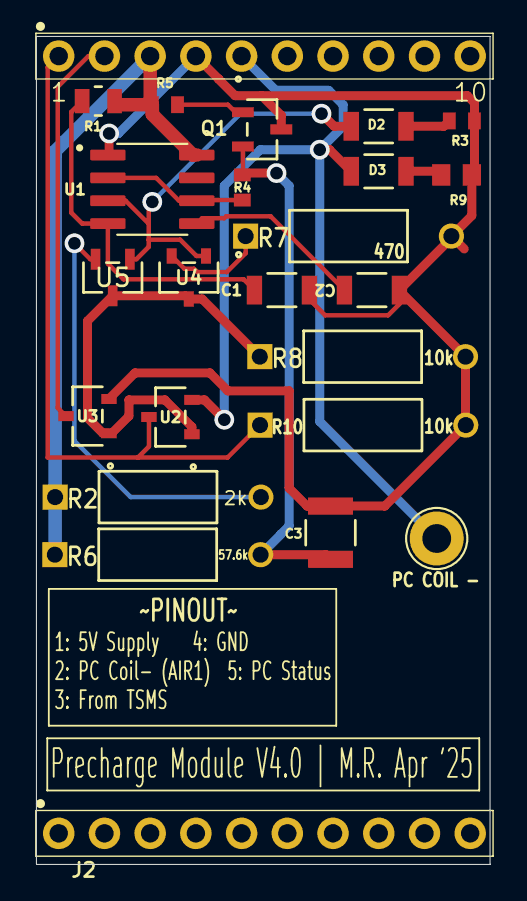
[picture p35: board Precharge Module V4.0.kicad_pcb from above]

Board: 2 copper layers, 25.2 x 46.0 mm, 24 parts (0 on the bottom side), 16 nets.

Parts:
C1, C2: 0.1u; CAP_CL31_SAM
C3: 47u; CAP_CL32_SAM
D2: 3 second timer; LED_AP3216SYD_KNB
D3: LED (Test); LED_AP3216SYD_KNB
J1, J2: PH1-10-UA; 1X10-2.54MM-THT
PC COIL -: TestPoint; TestPoint_Loop_D2.60mm_Drill1.6mm_Beaded
Q1: SS8550; SOT-23_MCC
R1: 22k; STA_RMCF0805_STP
R2: 2k; STA_CF14_STP
R3, R4, R5: 1k; STA_RMCF0603_STP
R6: 57.6k; STA_CF14_STP
R7: 470; STA_CF14_STP
R8, R10: 10k; STA_CF14_STP
R9: 150R; RC0805N_YAG
U1: NE555D; SOIC127P599X175-8N
U2, U3, U4: IRLML2060TRPBF; SOT23_INF
U5: PMV160UP_NEX

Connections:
Drain: R8.1, U2.1 (G), U3.1 (G), U4.3 (D), U5.3
END: D3.2 (A), J1.5, PC COIL -.1, U2.2 (S)
Gate: D2.2 (A), U1.3 (Q), U4.1 (G), U5.1
unnamed: D2.1 (K), R3.1
unnamed: D3.1 (K), R9.2
unnamed: Q1.1 (B), R5.2
unnamed: C1.2, C2.2, C3.2, J1.4, Q1.3 (C), R3.2, R7.2, R8.2, R9.1, R10.2, U1.1 (GND), U3.2 (S)
unnamed: C3.1, Q1.2 (E), R4.2, R6.2
unnamed: C2.1, U1.5 (CV)
unnamed: C1.1, R1.1, U1.4 (R)
unnamed: R4.1, U1.2 (TR), U1.6 (THR)
unnamed: J1.3, R1.2, R2.1, R5.1, R6.1, U1.8 (VCC)
unnamed: J1.1, U2.3 (D)
unnamed: J1.2, U3.3 (D)
NmosSource: R7.1, U4.2 (S)
PMOSSOURCE: R2.2, U5.2

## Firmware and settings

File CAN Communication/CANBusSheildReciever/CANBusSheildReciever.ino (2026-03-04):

#include <SPI.h>
#include <mcp_can.h>

const int SPI_CS_PIN = 9;   // Seeed Studio Shield uses D9
MCP_CAN CAN(SPI_CS_PIN);

void setup() {
  Serial.begin(115200);

  while (CAN.begin(MCP_ANY, CAN_500KBPS, MCP_8MHZ) != CAN_OK) {
    Serial.println("CAN init failed! Retrying...");
    delay(1000);
  }

  Serial.println("CAN initialized successfully!");
  CAN.setMode(MCP_NORMAL);
}

void loop() {
  if (CAN.checkReceive() == CAN_MSGAVAIL) {

    unsigned long rxId;
    byte len = 0;
    byte buf[8];

    CAN.readMsgBuf(&rxId, &len, buf);

    Serial.println("------ CAN Message Received ------");

    Serial.print("ID: 0x");
    Serial.println(rxId, HEX);

    Serial.print("Length: ");
    Serial.println(len);

    Serial.print("HEX Data: ");
    for (int i = 0; i < len; i++) {
      if (buf[i] < 0x10) Serial.print("0");  // leading zero
      Serial.print(buf[i], HEX);
      Serial.print(" ");
    }
    Serial.println();

    Serial.print("ASCII: ");
    for (int i = 0; i < len; i++) {
      if (isPrintable(buf[i])) {
        Serial.print((char)buf[i]);
      } else {
        Serial.print(".");
      }
    }
    Serial.println();

    Serial.println("----------------------------------\n");
  }
}

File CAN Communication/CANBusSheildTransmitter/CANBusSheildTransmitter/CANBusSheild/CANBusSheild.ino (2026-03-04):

#include <SPI.h>
#include <mcp_can.h>

const int SPI_CS_PIN = 9;     // CS pin for CAN shield
MCP_CAN CAN(SPI_CS_PIN);       // Create CAN object

const int CAN_ID = 0x100;      
const int BAUDRATE = CAN_500KBPS;  // Library uses predefined speeds

void setup() {
  Serial.begin(115200);

  if (CAN.begin(MCP_ANY, BAUDRATE, MCP_8MHZ) == CAN_OK) {
    Serial.println("CAN initialized successfully!");
  } else {
    Serial.println("CAN init failed!");
    while (1);
  }

  CAN.setMode(MCP_NORMAL);
}

void loop() {
  byte data[8] = {0,1,2,3,4,5,6,7};

  if (CAN.sendMsgBuf(CAN_ID, 0, 8, data) == CAN_OK) {
    Serial.println("Message Sent Successfully!");
  } else {
    Serial.println("Error Sending Message...");
  }

  delay(1000);
}

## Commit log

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2025-09-11 Hall Effect
    Added Hall Effect Circuit Files
    [PWM Module 3.0A-B_Cu.gbr, PWM Module 3.0A-B_Mask.gbr, PWM Module 3.0A-B_Paste.gbr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]
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2025-09-12 Hall Effect Board Changes
    Added a voltage divider to get to 2.5V, as there is not a VCU output which can do that - its toggleable by jumper cable, so if we have a better solution we don't need to make a new board to implement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
    Also moved pins to all be in the same row, since most of our boards are designed like that and it makes the overall board slightly less messy.
    [Hall Effect Sensor-B_Cu.gbr, Hall Effect Sensor-B_Mask.gbr, Hall Effect Sensor-B_Paste.gbr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]
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2025-09-13 Moved folders around
    Changed the op amp to a very similar one that can handle a 5V supply
    [Hall Effect Sensor.kicad_sch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]
2025-09-16 Added updated RTDS Kicad files
    [RTDS Control Module V4.0.kicad_pcb]
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2025-09-16 Kicad RTDS schematic changes
    [RTDS Control Module V4.0.kicad_sch]
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2025-09-24 Renaming stuff on boards that was wrong
    RTDS schematic was totally totally wrong with the pins compared to the PCB
    [AMS Latching Module V3.0.kicad_pcb, AMS Latching Module V3.0.kicad_sch, Circuit Power Module.kicad_sch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]
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2025-10-07 Changes to the io board mostly, put the old lv board in
    [LV Board Mk2.kicad_pcb, LV Board Mk2.kicad_sch, LV Board Mk2.step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]
2025-10-07 Symbol and Footprint Folder
    [VCU Charge Mode Signal Module V3.1.kicad_sch]
2025-10-21 LC Charge Circuit Schematic init
    [LVChargeNEW.kicad_pcb, LVChargeNEW.kicad_sch]
2025-10-21 IO board 3.0 files still need to change from 12 pin headers to 15 pin and add third PH connector for currently unsed pins
    [I-O Board V3.0.kicad_pcb, I-O Board V3.0.kicad_sch]
2025-10-21 Added LED, C and R footprints
    [LVChargeNEW.kicad_sch]
2025-10-21 IO board V3.0 fully done?
    [I-O Board V3.0.kicad_pcb]
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2025-10-24 5V and AMS Latch V1.0 Commit
    [5V AMS V1.0.kicad_pcb, 5V AMS V1.0.kicad_sch]
2025-10-26 VCU MPR & IMD Latch Commit - 26th October 2025
    [IMD Latching Module V3.0.kicad_pcb, VCU MPR & IMD Latch V1.0.kicad_pcb, VCU MPR & IMD Latch V1.0.kicad_sch]
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2025-10-28 fully updated on my end
    [5V AMS V1.0.kicad_pcb]
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2025-11-04 Revert "changes"
    This reverts commit 10df18be739a6716873fb9f13ef638a2302d6145.
    [Throttle Latching Module V3.1.kicad_pcb]
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2025-11-06 Added Csys and "thermistor" to GLV Charge ciruit
    Had to delete and re-add folder because of 4000 commits
    [LVChargeNEW.kicad_pcb, LVChargeNEW.kicad_sch]
2025-11-06 Precharge added to VCU Throttle Latching
    Precharge Module
    [VCUThrottleLatching.kicad_pcb, VCUThrottleLatching.kicad_sch]
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2025-11-07 Precharge module added along with file name change
    Precharge module added along with file name change
    [Throttle Latching Module V3.1-B_Cu.gbr, Throttle Latching Module V3.1-B_Mask.gbr, Throttle Latching Module V3.1-B_Paste.gbr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]
2025-11-11 got carried away and made a new VCU throttle latching
    [VCUThrottleLatching.kicad_pcb, VCUThrottleLatching.kicad_sch]
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2025-11-11 changes to the traces files and added new components for the fuse and connector.
    [3568.step, 691137710002.step, Traces V1.0.kicad_pcb]
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2025-11-12 getting dimensions correct for 5V AMS
    [5V AMS V1.0.kicad_pcb]
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2025-11-13 idk i cant revert it so its fine i guess
    [IO Module V2.0.kicad_pcb]
2025-11-13 PCB cleanup and retrace
    PCB cleanup and retrace
    [5V AMS V1.0.kicad_pcb, 5V AMS V1.0.kicad_sch]
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2025-11-13 VCU Latch and Precharge Schematic Update + Footprint Adjustments
    [DPAK-3_6P35X6P73_ONS.iges, VCUThrottleLatching.kicad_pcb, VCUThrottleLatching.kicad_sch]
2025-11-14 Revert "now IO should be done (fingers crossed)"
    This reverts commit 0e71786429b188e83ce6d05af818c70c1a18e264.
    [I-O Board V3.0.kicad_sch]
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2025-11-14 made layout smaller to have space for hall effect and added better silkscreen
    [VCUThrottleLatching.kicad_pcb]
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2025-11-14 3D models for LEDs fixed
    [VCUThrottleLatching.kicad_pcb]
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2025-11-14 Changed file name of VCU Throttle Latching to Throttle Latching Module, attempt to make VCU MPR & IMD Latch into IMD Latch & AMS Latch.
    [DPAK-3_6P35X6P73_ONS.iges, I-O Board V3.0.kicad_pcb, I-O Board V3.0.kicad_sch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]
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2025-11-14 fixed some silkscreen issues
    [VCU Signals.kicad_pcb]
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2025-11-14 traces board changed to add VCU MPR - 5V connections
    [Traces V1.0.kicad_pcb, Traces V1.0.kicad_sch]
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2025-11-14 rotated JST PH 12 it may not match the schematic exactly but it is correct electrically.
    [Traces V1.0.kicad_pcb]
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2025-11-14 GLV Charge PCB touch ups
    Fixed stray traces, pin headers (?)
    [LVChargeNEW.kicad_pcb]
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2025-12-02 Revert "changes that can probably be overriden?"
    This reverts commit 98343f344ad0564068fa41cd25b8ec5d82cca4ea.
    [Block Diagram.kicad_pcb, Block Diagram.kicad_sch, IMD & AMS Latches V1.0.csv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]
2025-12-02 Reapply "changes that can probably be overriden?"
    This reverts commit 4c938b53f4a382738003f7f338d558288f4e9314.
    [Block Diagram.kicad_pcb, Block Diagram.kicad_sch, IMD & AMS Latches V1.0.csv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]
2025-12-02 LV Charge fix cause I fucked it up
    [LVChargeNEW-B_Cu.gbr, LVChargeNEW-B_Mask.gbr, LVChargeNEW-B_Paste.gbr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]
2025-12-02 ok i fixed it
    [Block Diagram.kicad_pcb, Block Diagram.kicad_sch, Shutdown.kicad_pcb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]
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2025-12-02 Added 3-D models to VCUMPR5V
    Added 3-D models to VCUMPR5V
    [3587.step, ALF1PF12.STEP, LT1117CST-5_TRPBF.step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]
2025-12-02 Capacitor Added to 3-D models folder
    Capacitor Added to 3-D models folder
    [CL32B106KBJNNNE.step]
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2025-12-04 Added 3Dmodels to VCUMPR 5V
    Added 3Dmodels to VCUMPR 5V
    [VCU MPR - 5V V1.0.kicad_pcb]
2025-12-04 traces fixing pt 1
    [Traces V1.0.kicad_pcb]
2025-12-04 added pin header Models to most boards
    d pin header Models to most boards
    [I-O Board V3.0.kicad_pcb, IMD & AMS Latches V1.0.kicad_pcb, VCU MPR - 5V V1.0.kicad_pcb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]
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2026-01-26 Not sure what changed, probably just opening a file
    [Motherboard Test.kicad_pcb]
2026-01-27 80uf fix
    [LVChargeNEW.kicad_pcb, LVChargeNEW.kicad_sch]
2026-01-27 Traces Board Trace Makeover
    Traces Board Trace Makeover
    [Traces V1.0.kicad_pcb]
2026-01-27 added new SMD footprints, still some routing to do
    [LVChargeNEW.csv, LVChargeNEW.kicad_pcb, LVChargeNEW.kicad_sch]
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2026-01-28 fixed more 80uF caps
    [LVChargeNEW.kicad_pcb, LVChargeNEW.kicad_sch]
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2026-02-03 motherboard fixes
    [Motherboard Test.kicad_pcb]
2026-02-03 Update Precharge.kicad_sch
    Added 555 Timer to Precharge design. PMOS Orientation makes it look ugly but it's chill. The 1ms that the pmos for the optocoupler is on will not effect it because during the first ms the opamp outpu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
    [Precharge.kicad_sch]
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2026-02-06 added screw terminals and GLV- trace
    Haven't added any screw mount holes yet
    [Precharge.kicad_pcb, Precharge.kicad_sch]
2026-02-06 added mounting holes
    does HV- need to be traced?
    [Precharge.kicad_pcb, Precharge.kicad_sch]
2026-02-08 Added HV- Traces
    I believe everything is all set
    [Precharge.kicad_pcb]
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2026-02-16 Fixed precharge circuit
    problems with previous design (all my fault):
    1 - capacitor for the linear voltage regulator was connected between Vin and Adj, should be between Vin and ground
    2 - TS+ was being multiplied by 0.9 instead of HVPACK+
    3 - no resistor on the discharge pin of the 555 timer
    4 - 220 ohm resistor on linear voltage regulator would have made it output like 100V no bueno
    5 - if im not mistaken pin 2 and 6 of the 555 weren't connected???
    6 - some silkscreen stuff was ugly i guess so i fixed that
    [Precharge.kicad_pcb, Precharge.kicad_sch]
2026-02-17 found and fixed vias pointed out by the engineer
    [LVChargeNEW.kicad_pcb]
2026-02-17 added correct gerbers
    [LVChargeNEW-B_Cu.gbr, LVChargeNEW-B_Mask.gbr, LVChargeNEW-B_Paste.gbr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]
2026-02-18 AMS & IMD fixing some connections
    [IMD & AMS Latches V1.0-B_Cu.gbr, IMD & AMS Latches V1.0-B_Mask.gbr, IMD & AMS Latches V1.0-B_Paste.gbr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]
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2026-02-20 Fixed LVCharge discrepancies, may need to change footprints
    R1: 100k --> 1Meg (says 1000k) on datasheet
    R4: 100k --> 10
    C6, C7 100uF --> 100nF
    R20 should be removed
    [LVChargeNEW.kicad_sch]
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2026-03-12 flipped connectors
    [Traces V1.0.kicad_pcb]
2026-03-26 fixed naming mistake.
    MPR -> MPRD
    [VCU MPR - 5V V1.0.kicad_sch]
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

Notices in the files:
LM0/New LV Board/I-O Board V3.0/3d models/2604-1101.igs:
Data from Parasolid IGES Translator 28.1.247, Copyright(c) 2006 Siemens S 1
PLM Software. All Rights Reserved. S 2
